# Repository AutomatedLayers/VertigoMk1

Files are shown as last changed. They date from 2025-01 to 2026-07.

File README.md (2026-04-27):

# VertigoMk1
## Automation for Makers

Vertigo Mk1 is a 3D printer designed for automation. Some of its distinct features include:
- A bed that rotates to a vertical position and scrapes printed parts off and out the bottom
- Print queues, batch jobs, and remote failure recovery
- A small footprint compared to other automated part removal systems
- Scraper modules that use afforable plastic razors that are easy to replace and won't damage the print surface
- A height-adjustable scraper bar that can hold different scraper moodules - including those designed by YOU
- The ability to print and remove parts made with various materials
- Compatibility with different magnetic print surfaces, i.e. PEI, PEO, PEY, Garolite/FR4/G10, etc. 
- The easily swappable and serviceable Hitchcock toolhead
- A reciprocating filament cutter under the extruder that won't get stuck while cutting
- Compatibility with multi-material and automatic filament replacement systems
- An elecronics backpack that can be easily accessed and serviced
- Source-available hardware and open source software

[LINK TO BOM](https://docs.google.com/spreadsheets/d/1A0MQrvO-RssSD-6shnWwc1etPSYvOc4fTYE_1AOMABk/edit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)

[LINK TO DOCS](https://automatedlayers.github.io/VertigoMk1/)

## The STL files and BOM are released for beta testing. We welcome suggestions through GitHub's isssue tracker. During this phase of the project, there may be some updates to the STLs and BOM, so check the [STL change history](https://github.com/AutomatedLayers/VertigoMk1/commits/main/hardware/STL) and the [BOM change history](https://github.com/AutomatedLayers/VertigoMk1/commits/main/hardware/BOM.csv)
____________________________________________
# [Kickstarter Has Funded!](https://www.kickstarter.com/projects/automatedlayers/vertigo-mk1-the-evolution-of-automated-3d-printing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)



[AutomatedLayers.com](https://automatedlayers.com)

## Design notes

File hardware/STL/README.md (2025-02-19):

# Notes on printing these parts

This printer is designed to use ASA printed parts and we strongly recommend using ASA or ABS to print the majority of these parts. ASA is [comparable to ABS](https://all3dp.com/2/asa-vs-abs-differences). Other materials may work however YMMV. There are a few parts that should be printed with another material, i.e. translucent light diffusers. 

ASA and ABS shrink after printing. Remeber to calibrate your slicer scaling settings for your specific filament's rate of shrinkage. I.E. We scale our parts up by ~0.8% when printing with Polylite ASA

Under Construction...

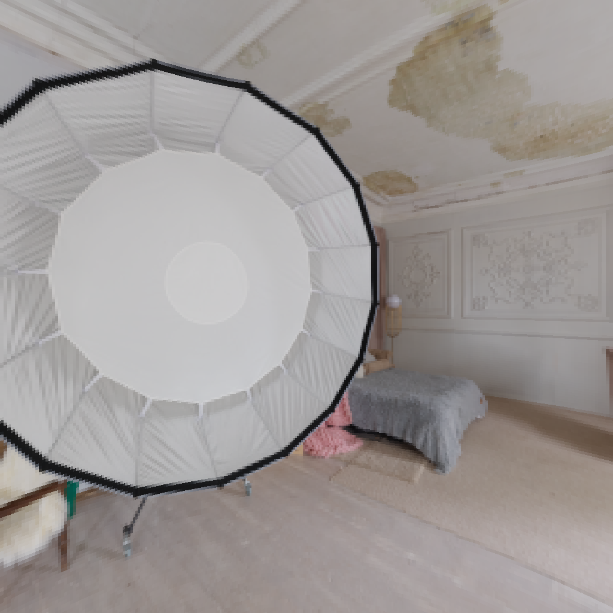
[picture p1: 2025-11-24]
docs/assets/js/o3dv/envmaps/studio/nx.png

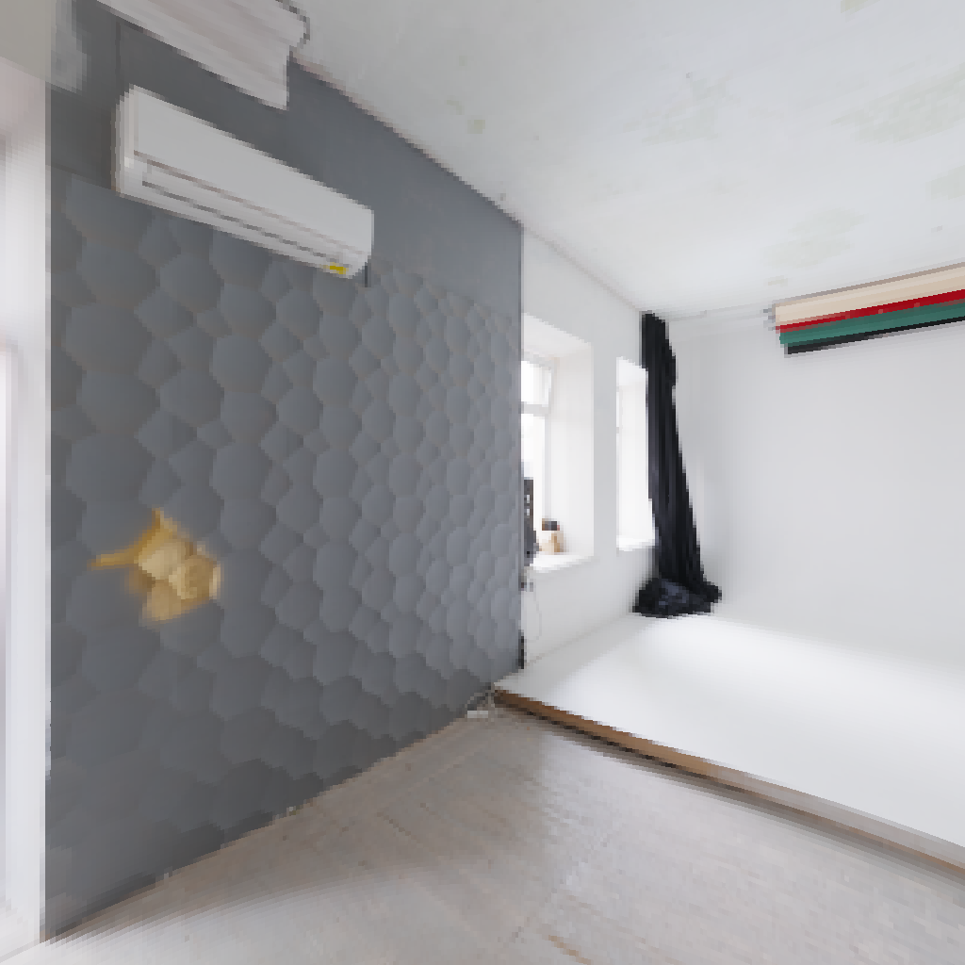
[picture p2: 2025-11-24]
docs/assets/js/o3dv/envmaps/studio/px.png

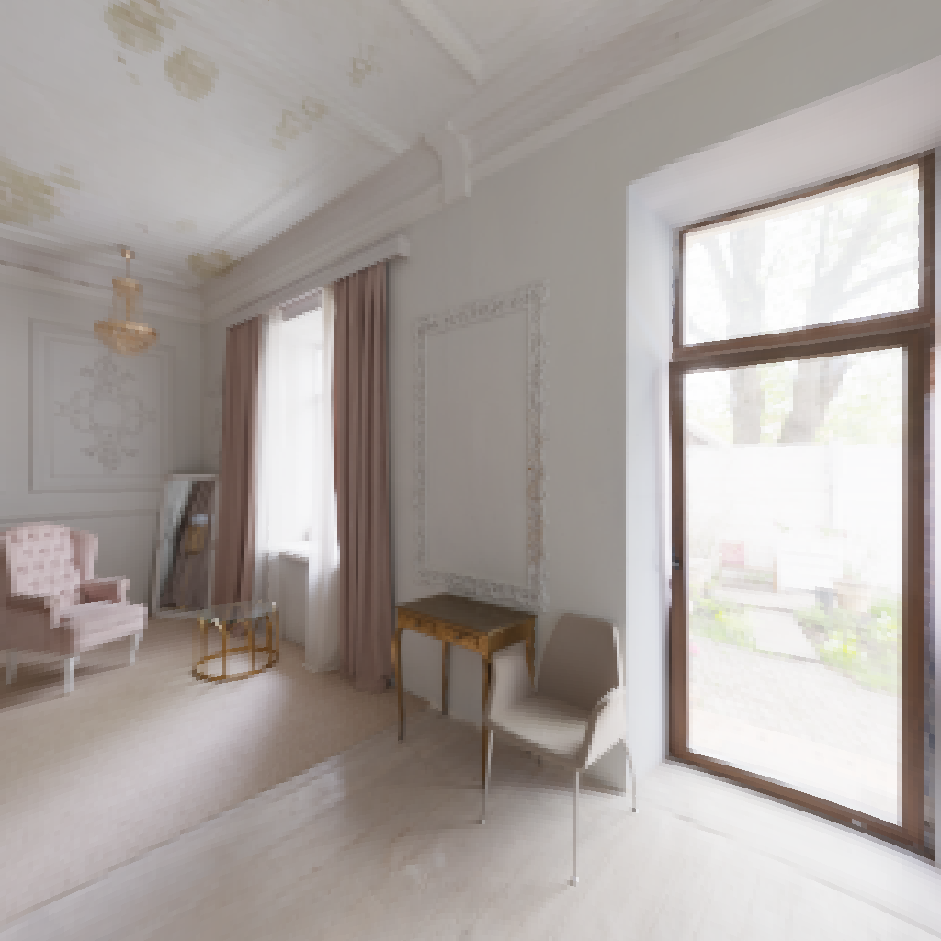
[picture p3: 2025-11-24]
docs/assets/js/o3dv/envmaps/studio/pz.png

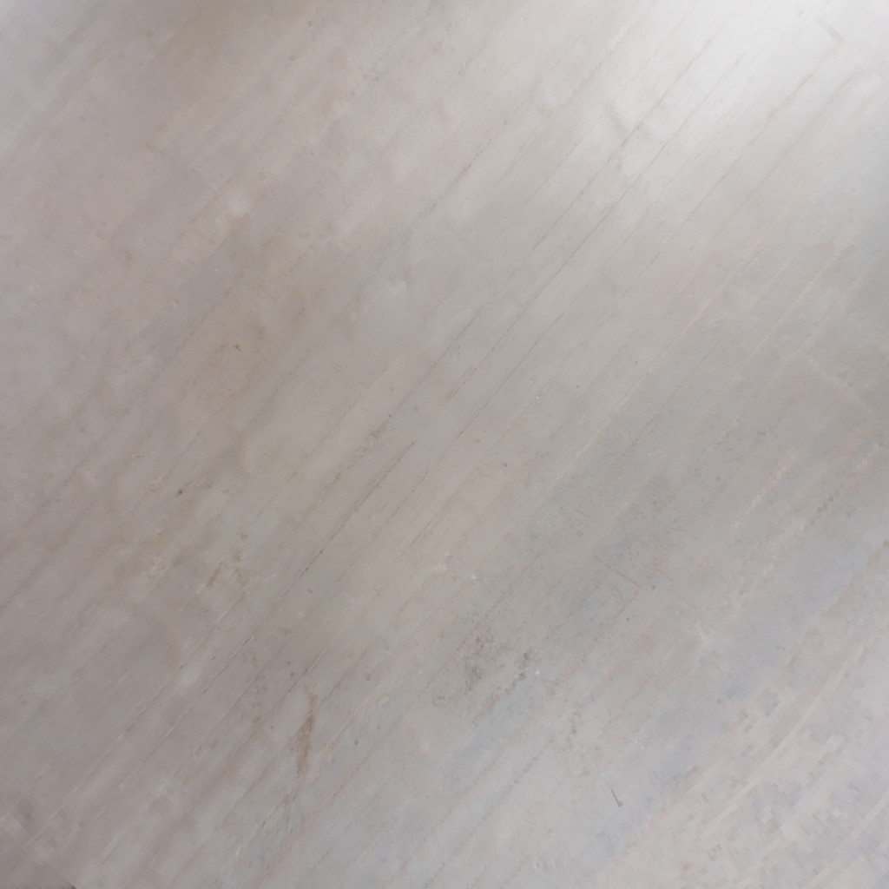
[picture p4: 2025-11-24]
docs/assets/js/o3dv/envmaps/studio/ny.png

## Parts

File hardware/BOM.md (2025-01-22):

[Link to BOM](https://docs.google.com/spreadsheets/d/10YGANyMZiwzZxh9XAjgCuSkIS7JlSp2upRrYD-nj4ag/edit?usp=sharing)

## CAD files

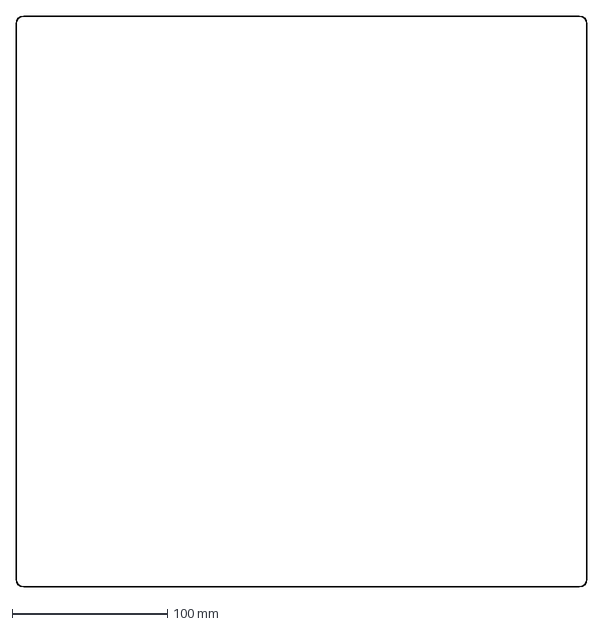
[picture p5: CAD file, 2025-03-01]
hardware/DXF/Top Panel.DXF
368.0 x 368.0 mm

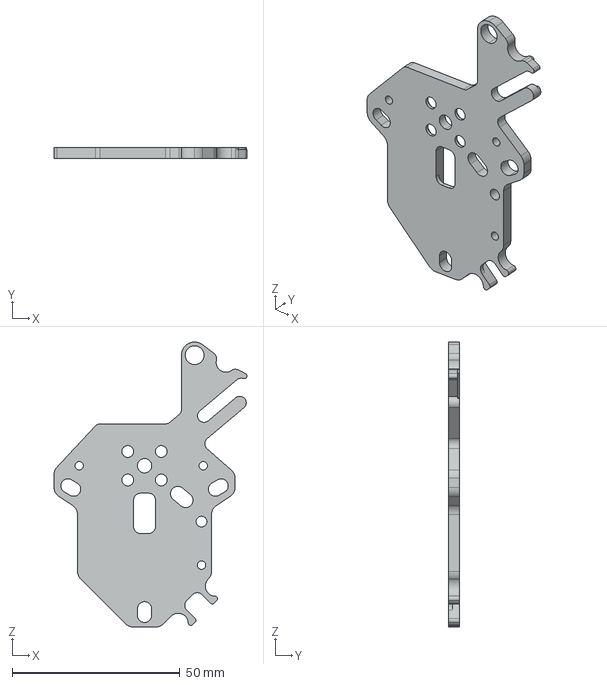
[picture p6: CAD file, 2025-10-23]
hardware/STEP/Toolhead Plate - CNC - Mild Steel 1045 - No Pockets - REV C.STEP
57.6 x 3.18 x 85.0 mm

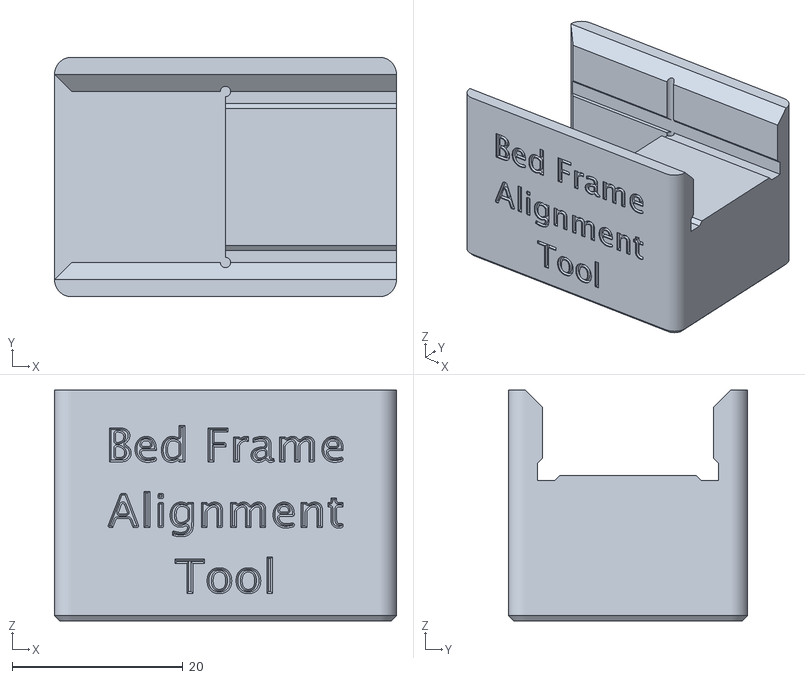
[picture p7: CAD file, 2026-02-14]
hardware/STL/00 Tools/Bed Frame Alignment Tool.stl
40.0 x 28.0 x 27.0

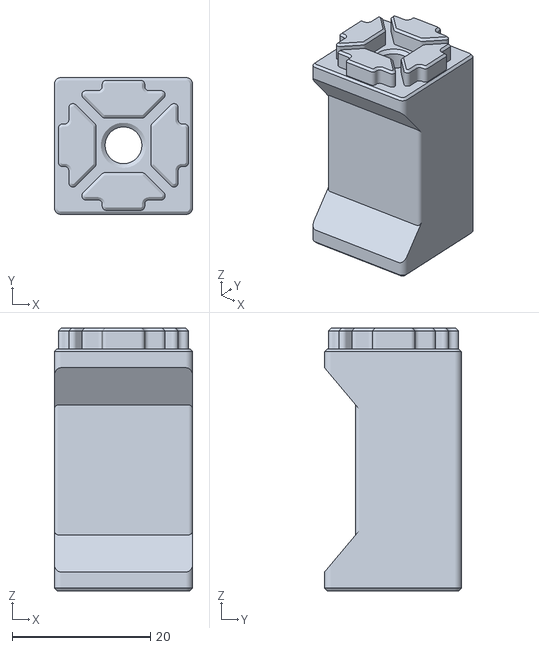
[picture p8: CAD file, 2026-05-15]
hardware/STL/01 Frame/Frame Post Connector - Q2 (LDO Profile).STL
20.0 x 19.8 x 38.0

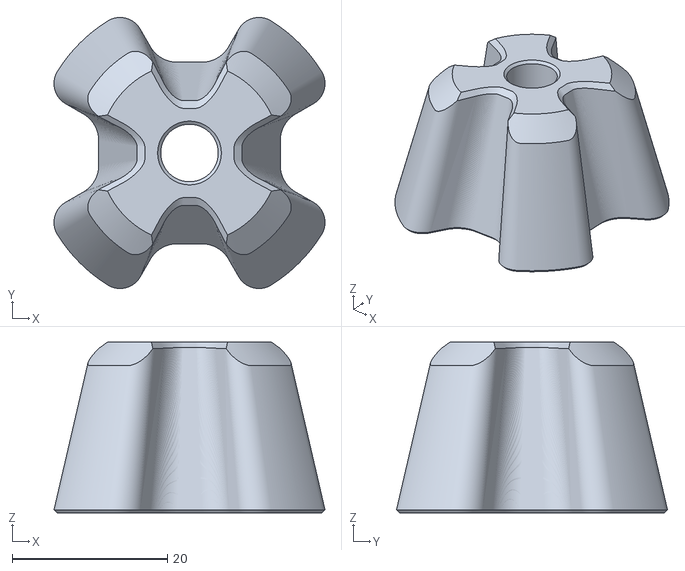
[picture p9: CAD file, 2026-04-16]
hardware/STL/02 Feet/All Feet/Foot Height Knob Cap - Accent - Q4.stl
34.9 x 34.9 x 22.0

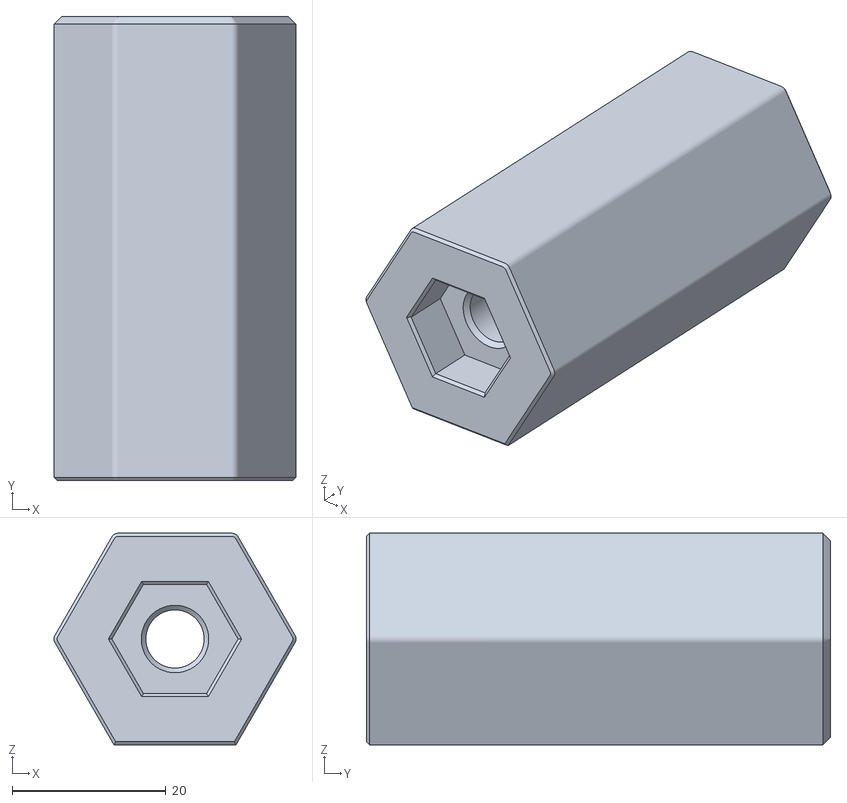
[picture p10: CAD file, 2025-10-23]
hardware/STL/02 Feet/Front Feet/Foot Front Replaceable Thread Plug - Q2.stl
31.4 x 60.3 x 27.5

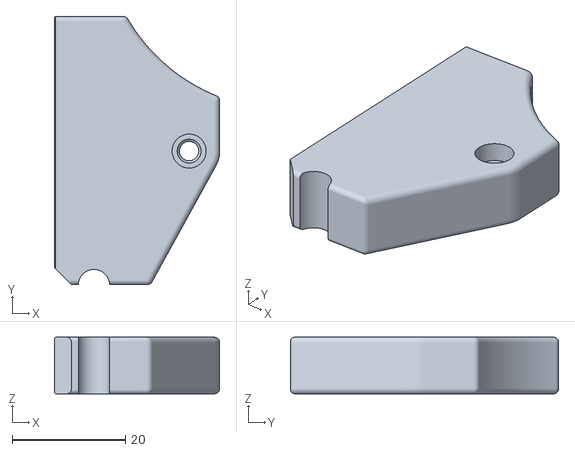
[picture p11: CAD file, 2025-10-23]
hardware/STL/02 Feet/Rear Feet/Foot Rear A Logo Nugget - Accent - Multi.stl
29.2 x 47.3 x 10.0

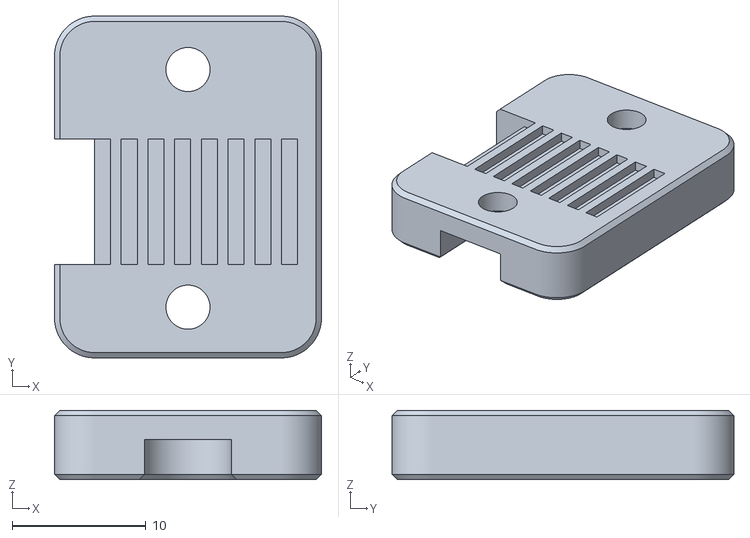
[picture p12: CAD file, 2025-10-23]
hardware/STL/03 Z Joints/Belt Clamps/Belt Clamp Top - Accent - Q4.stl
20.0 x 25.6 x 5.20

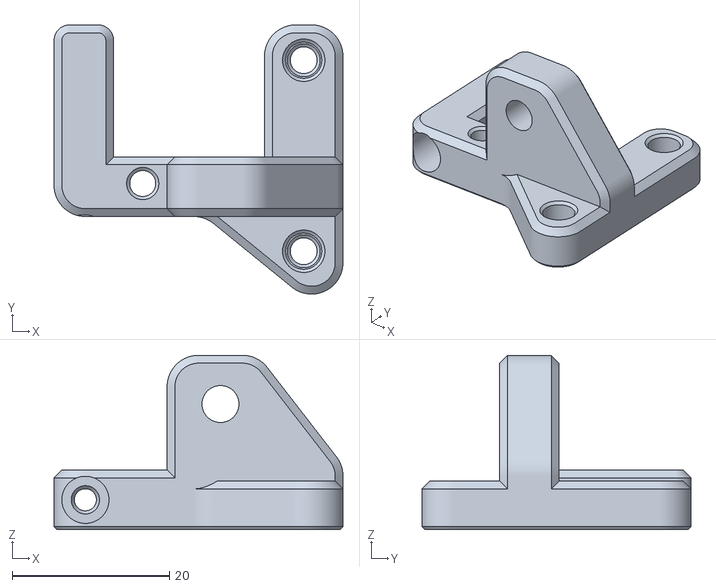
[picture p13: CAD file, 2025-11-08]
hardware/STL/03 Z Joints/Front Z Joints/Front Joint B - Endstop Adjustment.stl
36.8 x 34.3 x 22.2

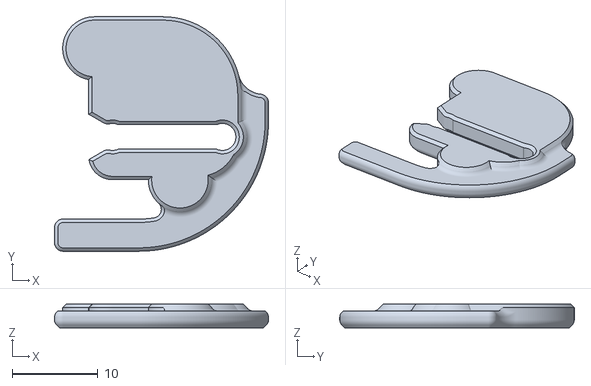
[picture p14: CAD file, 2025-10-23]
hardware/STL/03 Z Joints/Rear Z Joints/Rear Joint B - Seatbelt Lock B.stl
25.0 x 27.4 x 2.80

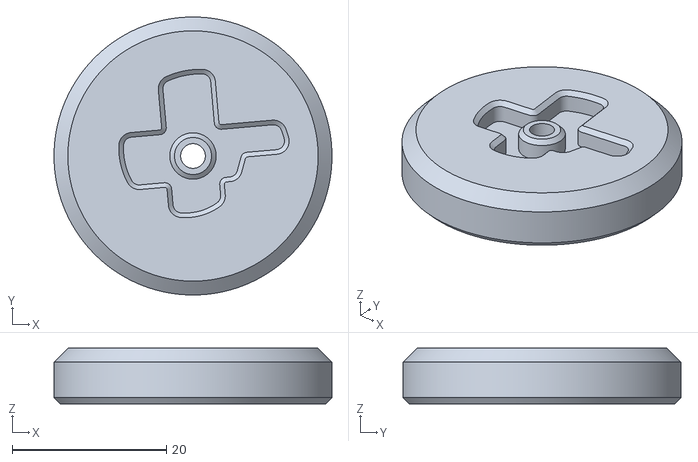
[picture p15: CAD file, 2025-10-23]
hardware/STL/04 XY Gantry/XY Drives/XY Drive B Cam Cap - Accent.stl
36.0 x 36.0 x 7.20

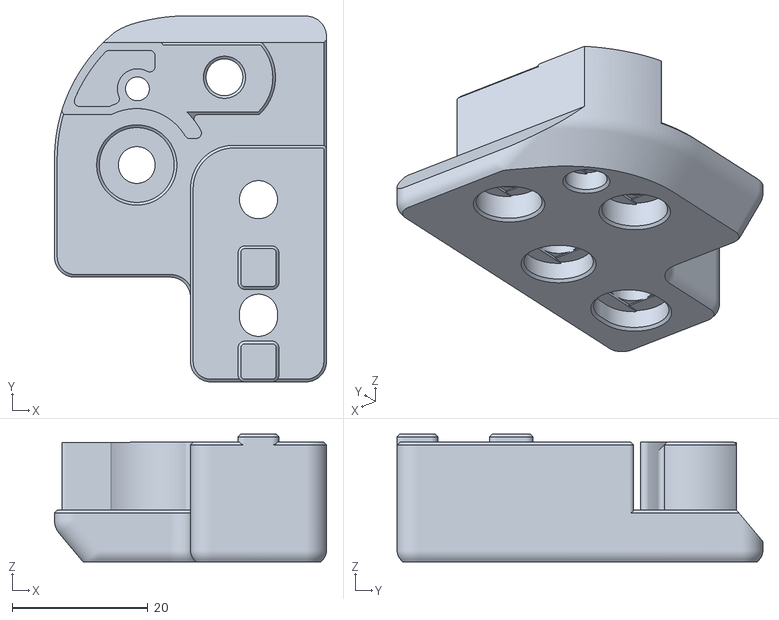
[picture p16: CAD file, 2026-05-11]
hardware/STL/04 XY Gantry/XY Joints/XY Joint B - Top.stl
40.0 x 53.8 x 18.8

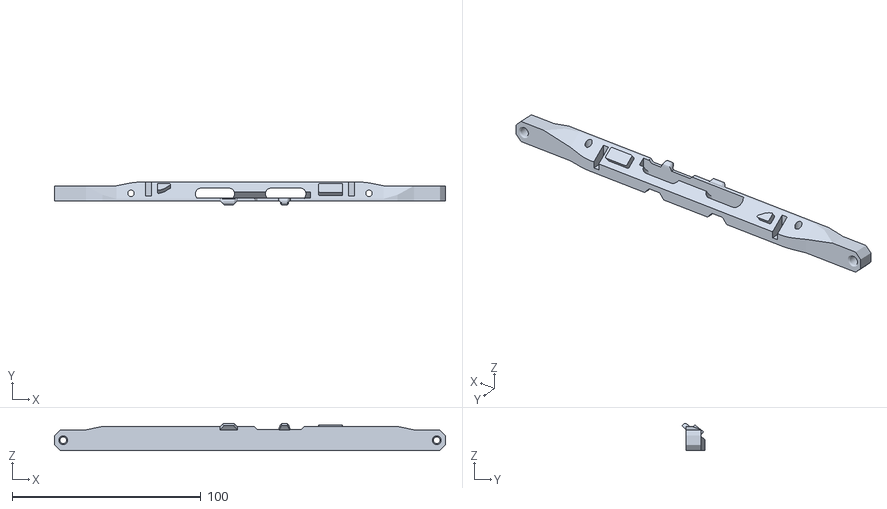
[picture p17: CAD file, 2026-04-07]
hardware/STL/05 Top Module/Camera and Logo Light/Logo LED & Camera Mount.stl
207.0 x 12.2 x 14.4

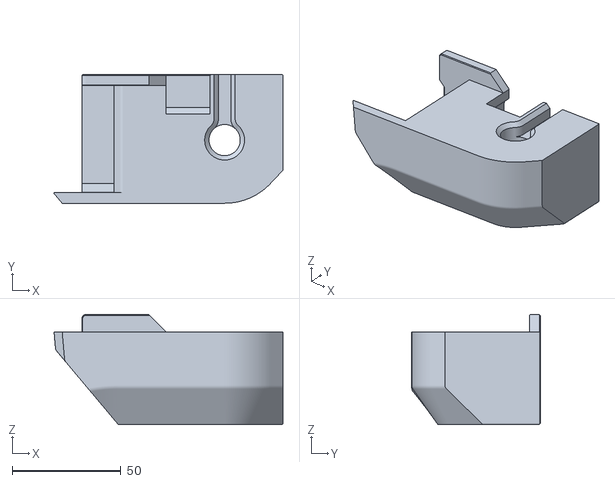
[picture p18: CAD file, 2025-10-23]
hardware/STL/05 Top Module/Facades/Motor Facade Front B.stl
105.1 x 59.0 x 50.6

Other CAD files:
hardware/STL/05 Top Module/Top Panel Plate/Top Panel Plate.stl
hardware/STL/05 Top Module/Z Drives/Z Drive Housing Cap B - Q2.stl
hardware/STL/06 Bed Platform/Bed Frame/Bed Frame - Tool Ball Mount B.stl
hardware/STL/06 Bed Platform/Scraper Bar/Scraper Bar Wing A.stl
hardware/STL/00 Tools/Bed Chain Cable Setter Tool.STL
hardware/STL/00 Tools/Force Sensor Washer Setting Tool.stl
hardware/STL/00 Tools/Frame Rear Bar Alignment Tool.STL
hardware/STL/00 Tools/Idler Bearing Tool.stl
hardware/STL/00 Tools/Light Bar Offset Tool.STL
hardware/STL/00 Tools/MGN9 Alignment Tool - Q2.STL
hardware/STL/00 Tools/Rear Foot Roll-In Nut Alignment Tool.STL
hardware/STL/00 Tools/XY Drive Roll-In Nut Alignment.STL
hardware/STL/00 Tools/Y-Rail Offset Tool.STL
hardware/STL/00 Tools/Z Drive Roll-In Nut Alignment Tool.STL
hardware/STL/01 Frame/Frame Post Connector - Q2 (Old).STL
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

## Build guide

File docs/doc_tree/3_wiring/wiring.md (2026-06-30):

---
title: Wiring
layout: default
nav_order: 3
zoom_images: true
---

# Wiring

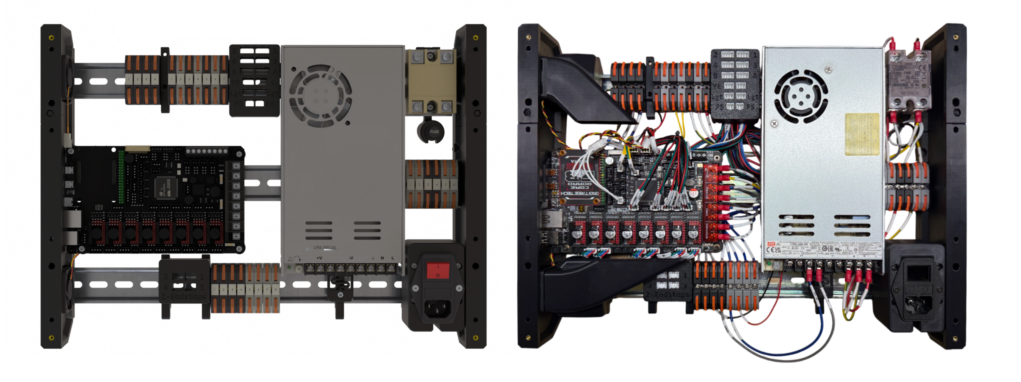
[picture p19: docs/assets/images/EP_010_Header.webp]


## Before You Start

The goal of this guide is to help you wire the printer carefully and consistently. That said, **electricity _can_ be dangerous**. Incorrect wiring or unsafe work practices can cause injury, damage components, start a fire, or worst of all, frighten your kitty. **You’ve got this — take your time, work safely, don’t skip steps, and double-check each step before moving forward.**

This printer is a DIY kit assembled from parts sourced from many suppliers across the world. Because of this, **hardware details may vary** between supplier batches or self-sourced parts. This can include component pinout, wire colors, connector styles, and other small differences. **Be careful about making assumptions based on appearance alone.** This guide provides the tools needed to verify each part, cable, and connection using the specification documents, which will be explained in the next section.

{: .important }
Some image text may appear small on this page. For a larger view, right-click the image and select "Open image in new tab".

{: .note}
[BigTreeTech Manta M8P V2 Documentation](https://github.com/bigtreetech/Manta-M8P/blob/master/V2.0/BIGTREETECH%20MANTA%20M8P%20V2.0%20User%20Manual.pdf) contains information related to the printer controller (mainboard). For convenience, here's the [M8P V2 Pinout]({{site.url}}/{{site.baseurl}}/assets/images/m8pv2_pinout.webp).

{: .note}
[Mellow FLY SHT36 V3 Documentation](https://mellow.klipper.cn/en/docs/ProductDoc/ToolBoard/fly-sht36/sht36_v3/) contains information related to the toolhead board. For convenience, here's the [FLY SHT36 V3 Pinout]({{site.url}}/{{site.baseurl}}/assets/images/sht36v3_pinout.webp)

## Table of Contents

- [Wiring](#wiring)
  - [Before You Start](#before-you-start)
  - [Table of Contents](#table-of-contents)
  - [Understanding the Wiring Diagram and Cable Spec](#understanding-the-wiring-diagram-and-cable-spec)
    - [The Cable Specification](#the-cable-specification)
      - [Cable Construction Examples](#cable-construction-examples)
    - [The Wiring Diagram](#the-wiring-diagram)
      - [Finding Z-Code Termination Points Example](#finding-z-code-termination-points-example)
  - [Diagrams of Peripheral-Board Connections, Z-Codes, and Schematic Labels](#diagrams-of-peripheral-board-connections-z-codes-and-schematic-labels)
  - [Configuring the Toolhead Board](#configuring-the-toolhead-board)
    - [Install Jumpers and Fan Mosfet and Set Switches (for CAN Mode) on Toolhead Board](#install-jumpers-and-fan-mosfet-and-set-switches-for-can-mode-on-toolhead-board)
  - [Wiring The Electronics Backpack](#wiring-the-electronics-backpack)
    - [1. Install CM and Heatsink](#1-install-cm-and-heatsink)
    - [2. Install Jumpers on Main Board](#2-install-jumpers-on-main-board)
    - [3. Install Stepper Drivers](#3-install-stepper-drivers)
    - [4. Install Terminal Block Bus Bars](#4-install-terminal-block-bus-bars)
    - [5. Install Terminal Block Bus Bar Fasteners](#5-install-terminal-block-bus-bar-fasteners)
    - [6. Install Terminal Block Number Covers](#6-install-terminal-block-number-covers)
    - [7. Check Fuse Amperage - IEC C14 Plug](#7-check-fuse-amperage---iec-c14-plug)
    - [8. Check Fuse Amperage - Bed Fuse (Z-07)](#8-check-fuse-amperage---bed-fuse-z-07)
    - [9. Check PSU's AC Input Voltage Switch](#9-check-psus-ac-input-voltage-switch)
    - [10. Install Cables: Z-01, Z-02, Z-03, Z-11, Z-12](#10-install-cables-z-01-z-02-z-03-z-11-z-12)
    - [11. Install Cables: Z-04, Z-05, Z-06](#11-install-cables-z-04-z-05-z-06)
    - [12. Prepare Multimeter for Continuity Checks](#12-prepare-multimeter-for-continuity-checks)
    - [13. Check for short between AC Live (L) and AC Neutral (N)](#13-check-for-short-between-ac-live-l-and-ac-neutral-n)
    - [14. Check for short between AC Neutral (N) and AC Earth (⏚)](#14-check-for-short-between-ac-neutral-n-and-ac-earth-)
    - [15. Check for short between AC Live (L) and AC Earth (⏚)](#15-check-for-short-between-ac-live-l-and-ac-earth-)
    - [16. Check for short between PSU's DC(+) and DC(-)](#16-check-for-short-between-psus-dc-and-dc-)
    - [17. Check for continuity between IEC C14 plug and PSU for AC Live (L)](#17-check-for-continuity-between-iec-c14-plug-and-psu-for-ac-live-l)
    - [18. Check for continuity between IEC C14 plug and PSU for AC Neutral (N)](#18-check-for-continuity-between-iec-c14-plug-and-psu-for-ac-neutral-n)
    - [19. Check for continuity between IEC C14 plug and PSU for AC Earth (⏚)](#19-check-for-continuity-between-iec-c14-plug-and-psu-for-ac-earth-)
    - [20. Preparing for First Power ON](#20-preparing-for-first-power-on)
    - [Always prioritize your safety and the safety of those around you](#always-prioritize-your-safety-and-the-safety-of-those-around-you)
    - [21. Adjusting PSU to 24V](#21-adjusting-psu-to-24v)
    - [22. Install Terminal Block Covers](#22-install-terminal-block-covers)
    - [23. Install Cables: Z-13, Z-15, Z-17, Z-19](#23-install-cables-z-13-z-15-z-17-z-19)
    - [24. Install Cables: Z-14, Z-16, Z-18, Z-20](#24-install-cables-z-14-z-16-z-18-z-20)
    - [25. Install Cables: Z-07, Z-08, Z-09, Z-10, Z-21, Z-22](#25-install-cables-z-07-z-08-z-09-z-10-z-21-z-22)
    - [26. Install Cables: Z-23, Z-24, Z-26](#26-install-cables-z-23-z-24-z-26)
    - [27. Assembling Peripheral Blocks](#27-assembling-peripheral-blocks)
    - [28. Install Cables: Z-42, Z-43, Z-44, Z-45](#28-install-cables-z-42-z-43-z-44-z-45)
    - [29. Install Cables: Z-27, Z-28](#29-install-cables-z-27-z-28)
    - [30. Install Cables: Z-34, Z-35, Z-32/33](#30-install-cables-z-34-z-35-z-3233)
    - [31. Install Cables: Z-29, Z-30, Z-31](#31-install-cables-z-29-z-30-z-31)
    - [32. Install Cables: Z-40, Z-41](#32-install-cables-z-40-z-41)
    - [33. Install Cables: Z-38, Z-39](#33-install-cables-z-38-z-39)
    - [34. Install Cables: Z-36, Z-37](#34-install-cables-z-36-z-37)
    - [35. Complete the Electronics Backpack Section then Continue](#35-complete-the-electronics-backpack-section-then-continue)
    - [36. Install Cables: Z-25, Z-48, Z-49, Z-53, Z-54, Z-55, Z-56, Z-60, Z-61, Z-114](#36-install-cables-z-25-z-48-z-49-z-53-z-54-z-55-z-56-z-60-z-61-z-114)
    - [37. Unplug Toolhead's XT30 Connector](#37-unplug-toolheads-xt30-connector)
    - [38. Checking Toolhead Power](#38-checking-toolhead-power)
    - [39. PZ Probe Controller Cable: Z-105, Z-106, Z-107](#39-pz-probe-controller-cable-z-105-z-106-z-107)
    - [40. Install Lights, Endstops, Electronics Fans, Camera: Z-57, Z-58, Z-59, Z-68, Z-69, Z-70, Z-71, Z-72, Z-77, Z-78, Z-116](#40-install-lights-endstops-electronics-fans-camera-z-57-z-58-z-59-z-68-z-69-z-70-z-71-z-72-z-77-z-78-z-116)
    - [41. Endstop Check](#41-endstop-check)
    - [42. Electronics Fans Pinout Check: Z-77, Z-78](#42-electronics-fans-pinout-check-z-77-z-78)
    - [43. Install Bed Heater, Bed Fans: Z-46, Z-47, Z-50, Z-51, Z-52](#43-install-bed-heater-bed-fans-z-46-z-47-z-50-z-51-z-52)
    - [44. Install Stepper Motors: Z-46, Z-47, Z-50, Z-51, Z-52](#44-install-stepper-motors-z-46-z-47-z-50-z-51-z-52)
  - [Continue to the Firmware Guide](#continue-to-the-firmware-guide)

## Understanding the [Wiring Diagram and Cable Spec](https://github.com/AutomatedLayers/VertigoMk1/tree/main/electrical/Cable%20Spec%20%26%20Wiring%20Diagram)

Wiring is defined by two core documents: the **wiring diagram** and the **cable specification**.

### The Cable Specification

This document defines how each cable is manufactured, including its Z-code, length, wire gauge, color, pinout, and other relevant build details.

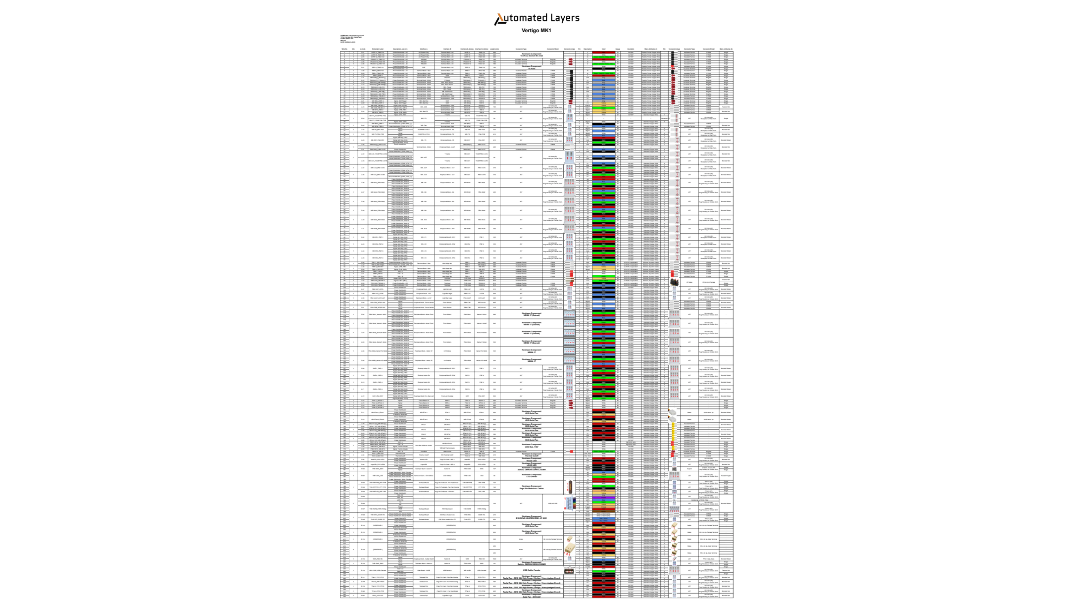
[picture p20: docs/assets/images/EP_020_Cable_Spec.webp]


<br>

#### Cable Construction Examples

Below are cables Z-11 and Z-36 as it appears in the cable specification, along with a photos of the construction for reference. Keep in mind that not every hardware component will have the physical Z-code label attached. In those cases, identify the cable by comparing its features to the cable specification, or consult the Wiring Diagram if you know where the component is being installed to easier identifiy the Z-code. 

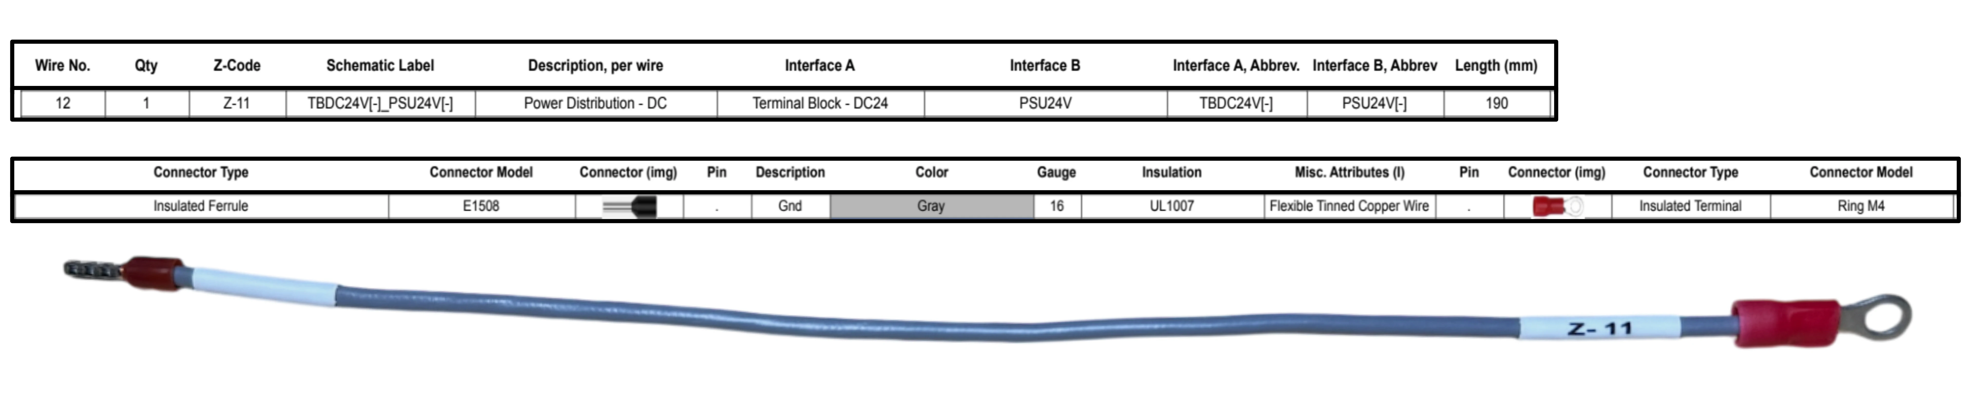
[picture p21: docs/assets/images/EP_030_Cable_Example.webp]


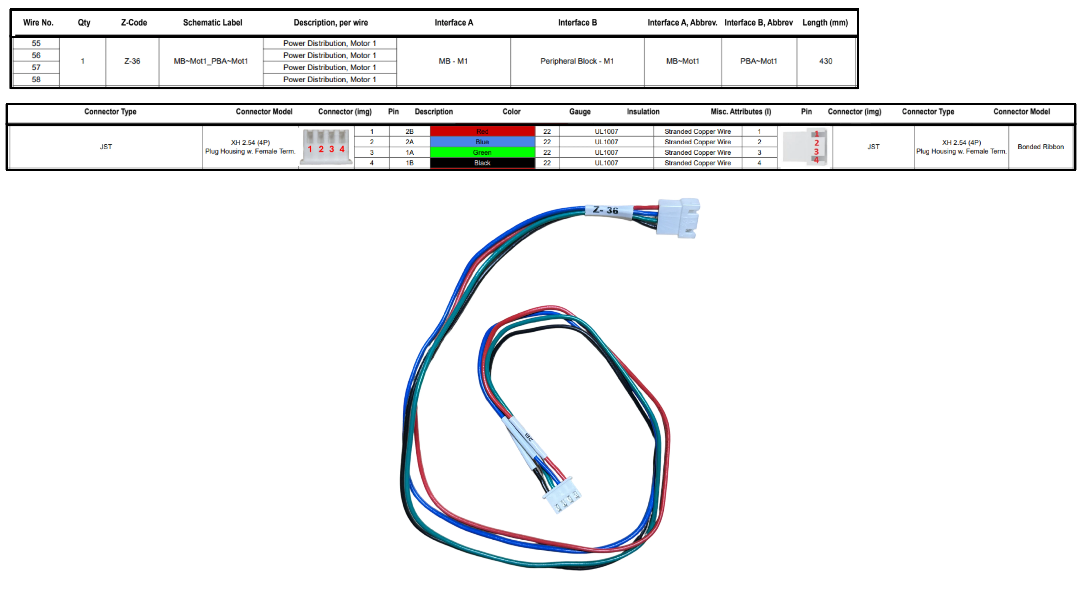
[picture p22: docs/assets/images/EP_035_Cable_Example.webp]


### The Wiring Diagram

This document defines how the cables terminate within the system, using symbols and Z-codes to identify connections.

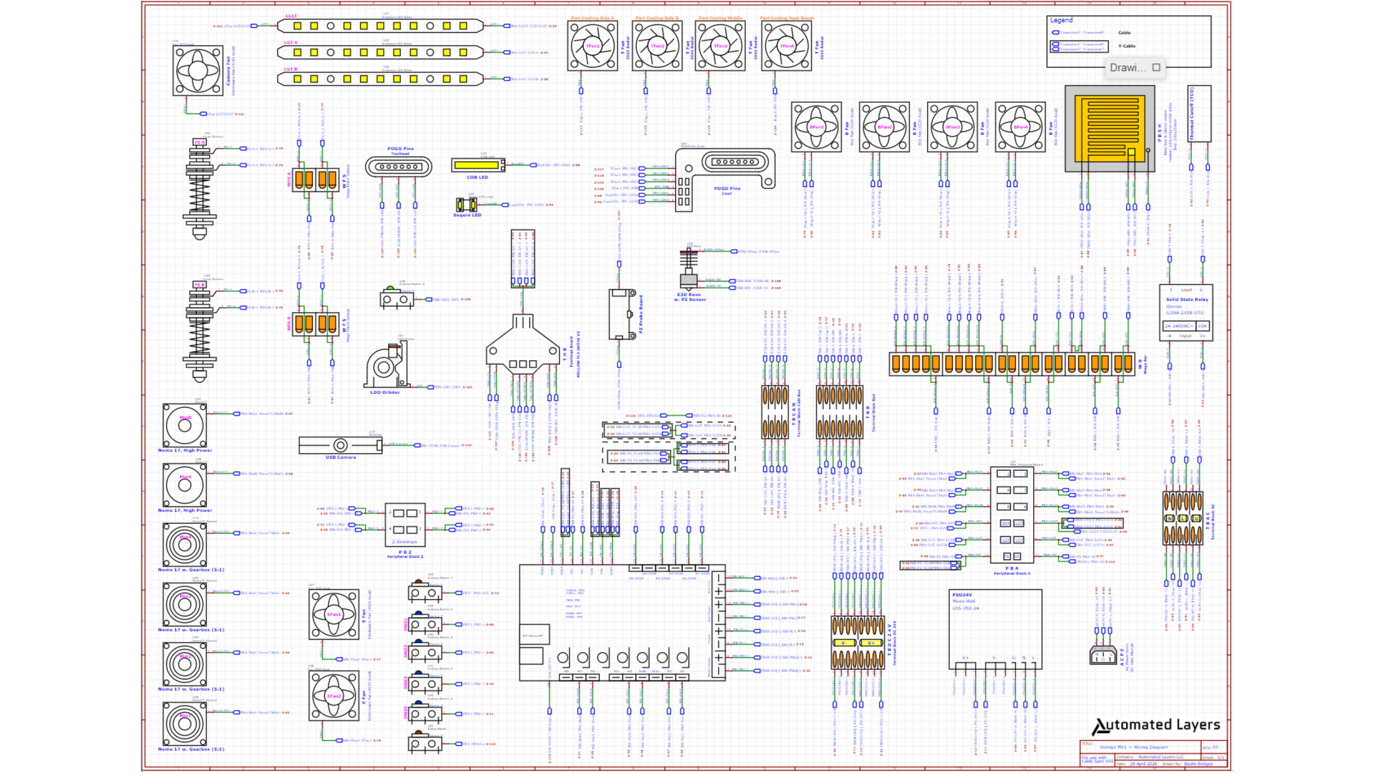
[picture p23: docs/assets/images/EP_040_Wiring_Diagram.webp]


<br>

#### Finding Z-Code Termination Points Example

* Locate the Z-Code: There will be one located at each termination point for the cable
* Note the schematic label: This indicates the termination points using abbreviated names, separated by an underscore "_"
  * E.g. Z-11, TBDC24V[-]_PSU24V[-] indicates you can find the termination points at Terminal Block DC 24V [-] and the Power Supply Unit 24V [-]

**Tip:** Opening the PDF and using the find function is an easy way to navigate the Z-Code termination points.

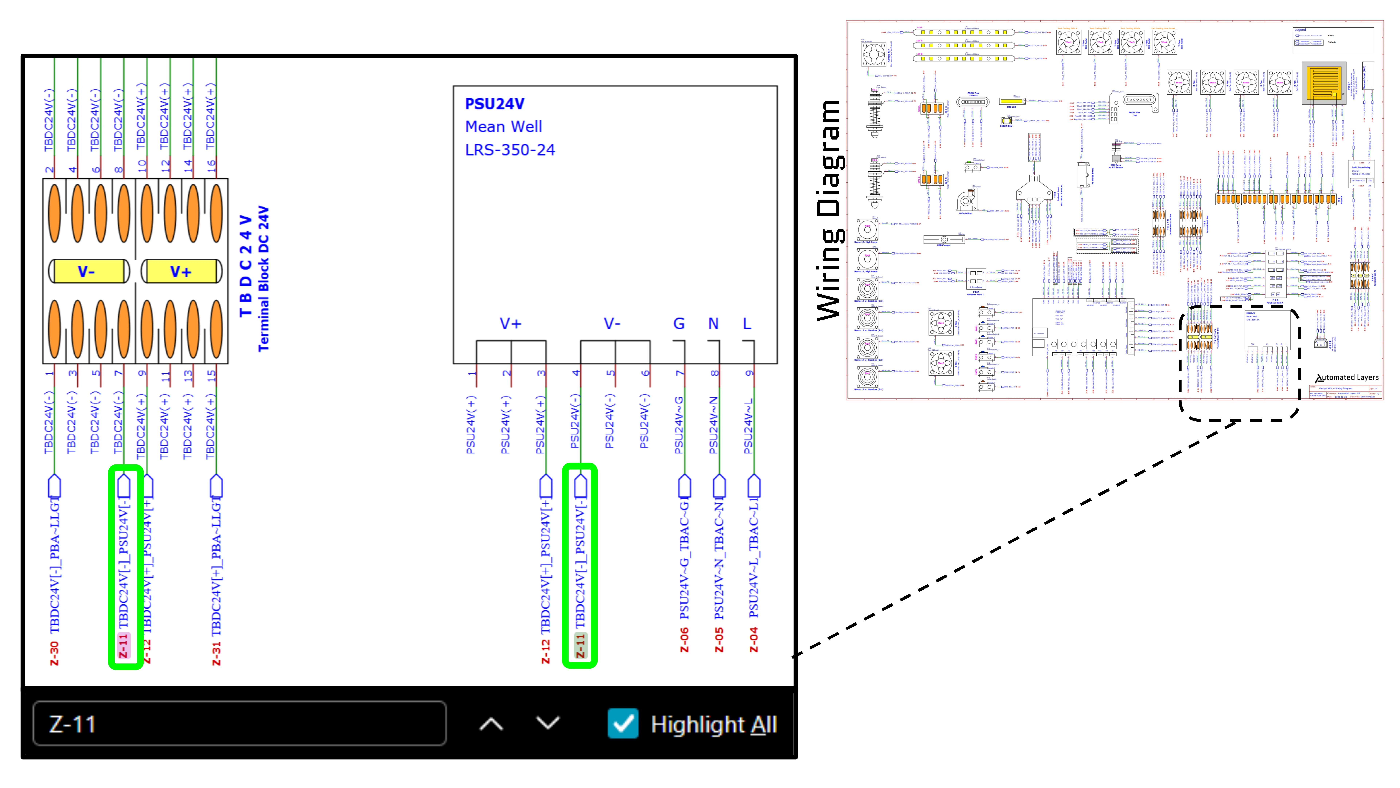
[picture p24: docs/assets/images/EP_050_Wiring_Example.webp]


{: .warning }
When using these documents, always perform a quick check to confirm that you are using the [latest revision](https://github.com/AutomatedLayers/VertigoMk1/tree/main/electrical/Cable%20Spec%20%26%20Wiring%20Diagram) before proceeding.

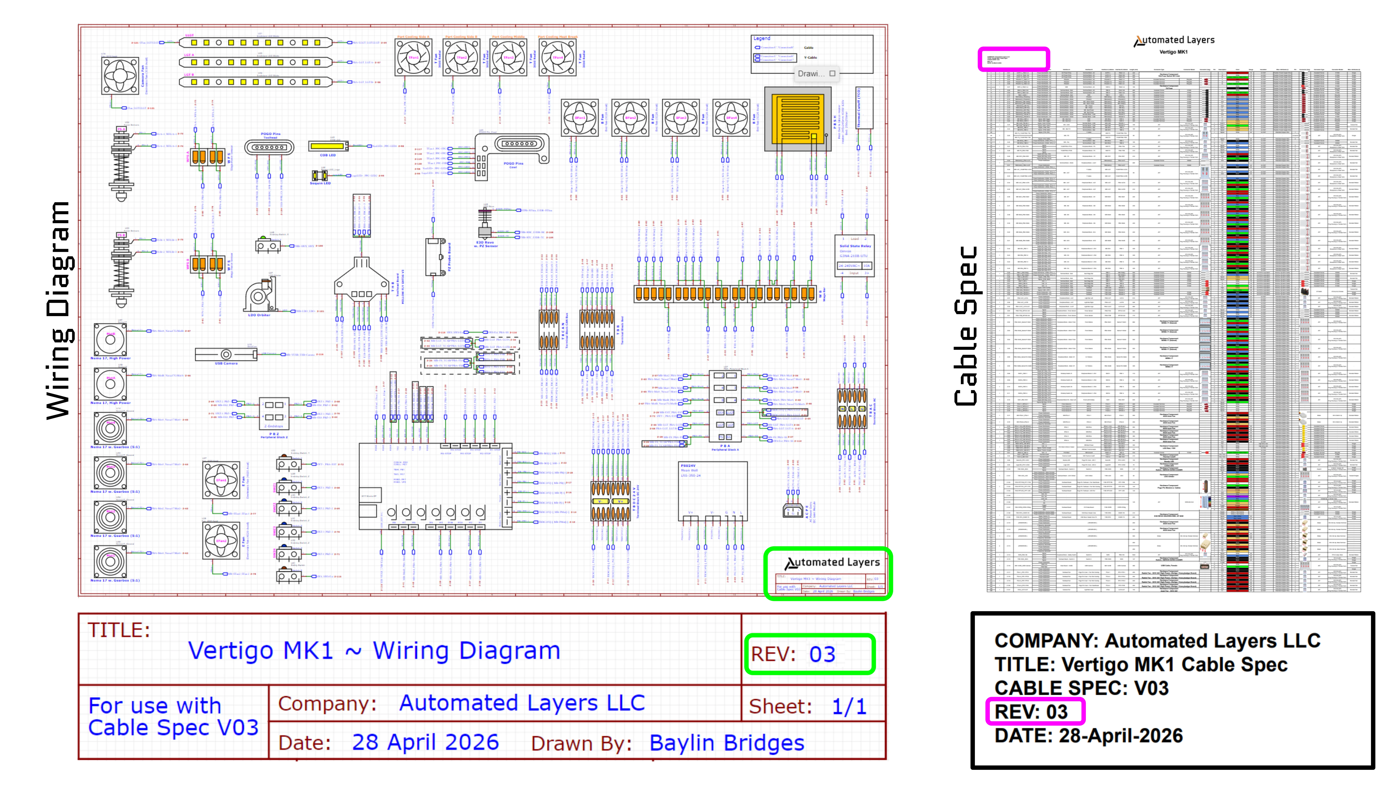
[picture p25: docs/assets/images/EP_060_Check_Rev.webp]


<br>

## Diagrams of Peripheral-Board Connections, Z-Codes, and Schematic Labels

<br>







<br>

[Return to Z Endstop assembly]({{site.url}}/{{site.baseurl}}/doc_tree/2_assembly/06_auxiliary_modules_1/1_z-endstops.html)

## Configuring the Toolhead Board

### Install Jumpers and Fan Mosfet and Set Switches (for CAN Mode) on Toolhead Board

* Toolhead fans are set to 24V
* Setting GPIO20 to 3.3V is optional, but recommended
* Fan Mosfet is installed (Mosfet can be installed either orientation; just ensure all 6 pins are inserted)
* Toolhead board is set to CAN mode with switches on back of board
* Set CAN Bus 120 Ohm terminal resistor to ON position

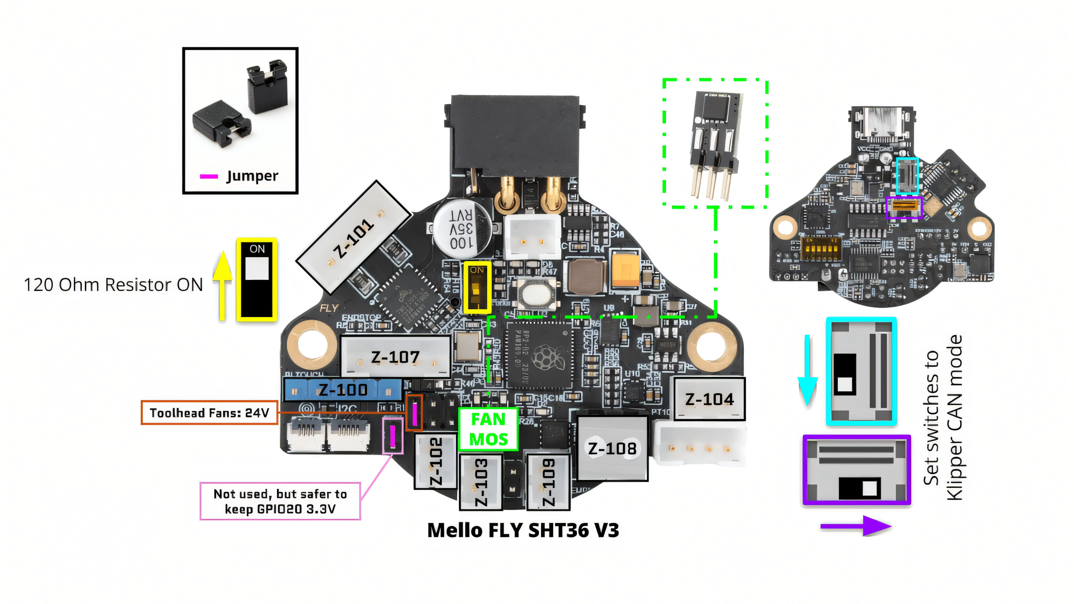
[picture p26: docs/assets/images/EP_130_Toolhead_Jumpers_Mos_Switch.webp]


[Return to Extruder Plate assembly]({{site.url}}/doc_tree/2_assembly/12_toolhead/1_extruder_plate.html)

## Wiring The Electronics Backpack

<!-- ### If this is your first visit, you are arriving from "[Assembly - Electronics Backpack - Vertigo MK1](https://youtu.be/X98VDksNd48?si=4Hsjn2eWTSBX0ba6)"

![]({{site.url}}/{{site.baseurl}}/assets/images/EP_090_Youtube_Electronics_Backpack.webp) -->

### 1. Install CM and Heatsink

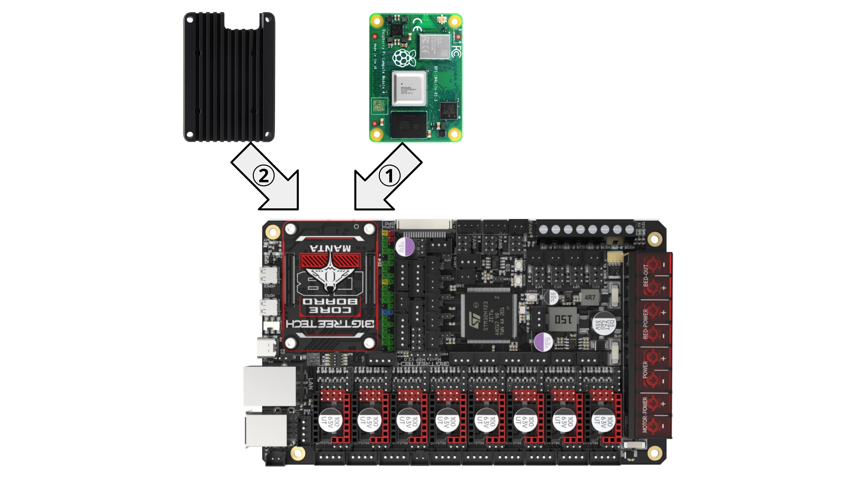
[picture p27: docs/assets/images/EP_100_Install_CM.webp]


### 2. Install Jumpers on Main Board

**Jumpers are used to select the following settings:**

* All stepper drivers are set to 24V
* TMC5160T Pro drivers are set to SPI mode
* TMC2209 drivers are set to UART mode
* Bed fans are set to 24V
* E-Panel fans are set to 24V
* Enclosure LEDs are set to 24V
* CAN Bus 120 ohm jumper is installed (*smaller jumper than the others)

{: .warning }
Double-check all jumper settings before applying power — an incorrect configuration can permanently damage the board (the kind that can't be undone). We can tell you from experience an extra or misplaced jumper makes for a good firework show. 

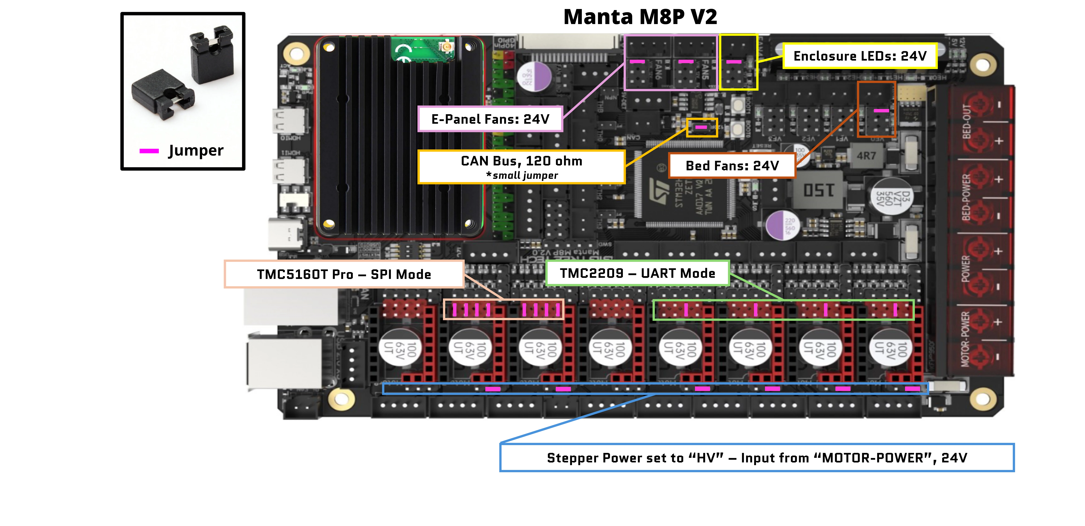
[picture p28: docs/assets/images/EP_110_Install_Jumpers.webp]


### 3. Install Stepper Drivers

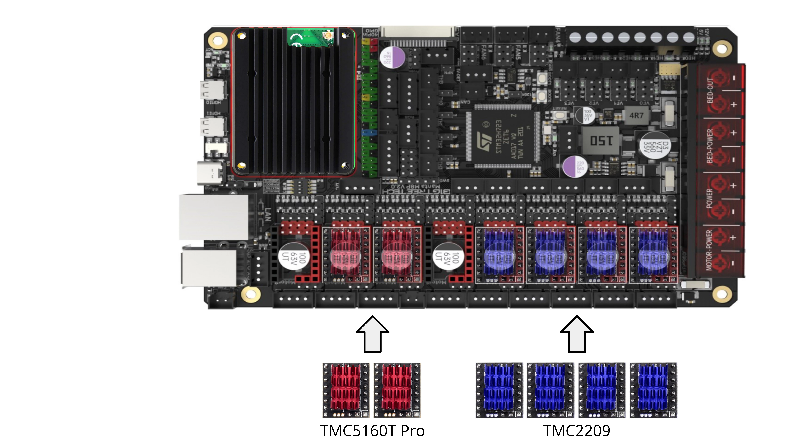
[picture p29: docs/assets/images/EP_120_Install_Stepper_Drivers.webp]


### 4. Install Terminal Block Bus Bars

* Cut terminal block bus bars to length
* Trim excess material from where the cut was made
* Install bus bars in terminal blocks as shown

{: .warning }
Double-check that each bus bar is cut to the correct node length. Trim any excess material between bus bars so they are not close to touching. When finished, it should match the image above.

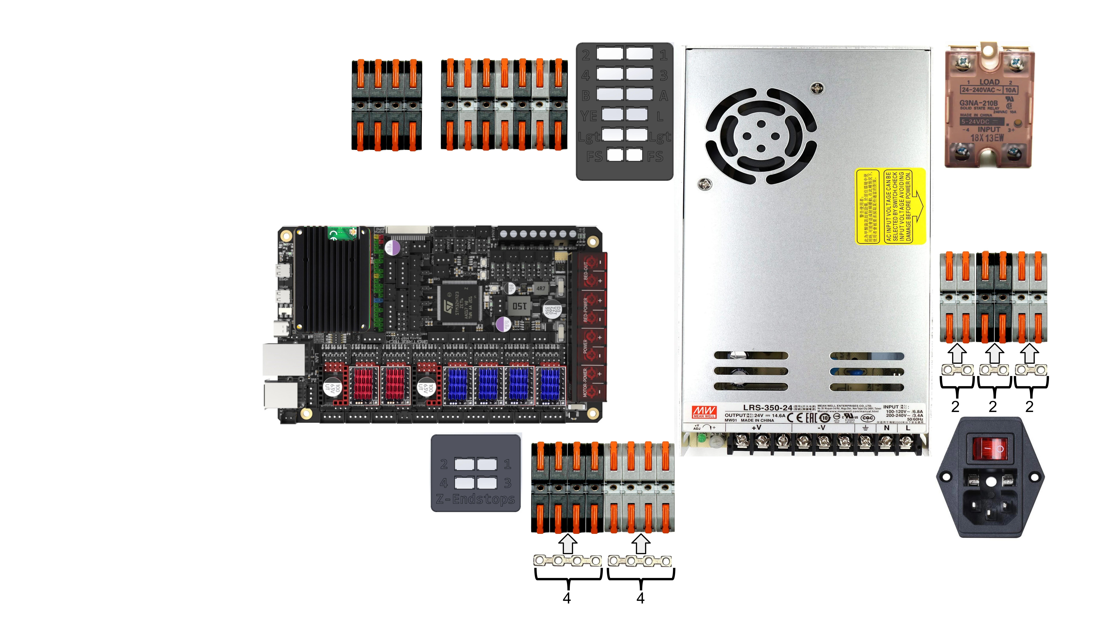
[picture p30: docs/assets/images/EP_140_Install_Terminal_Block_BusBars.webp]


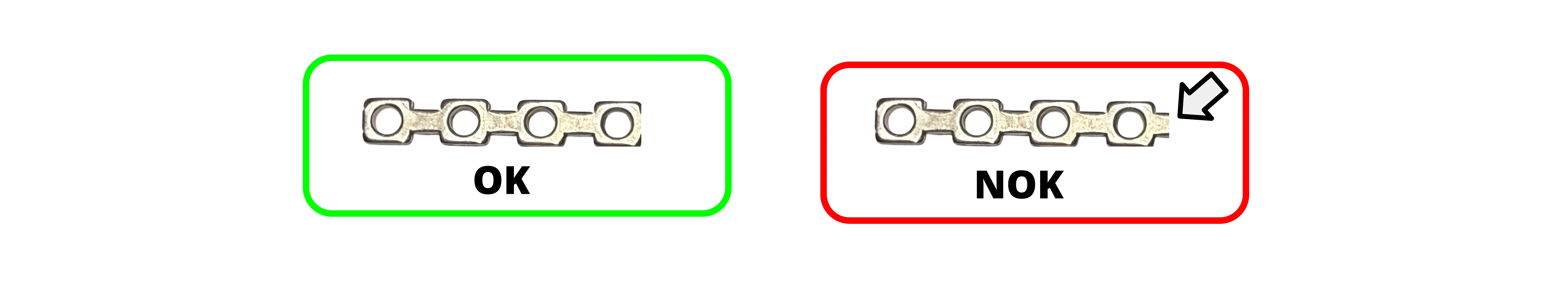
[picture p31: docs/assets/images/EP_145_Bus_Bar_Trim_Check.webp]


### 5. Install Terminal Block Bus Bar Fasteners

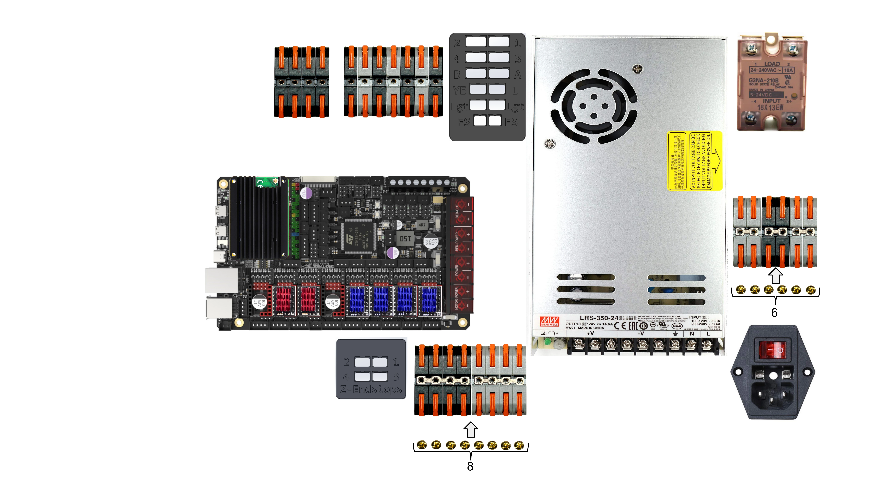
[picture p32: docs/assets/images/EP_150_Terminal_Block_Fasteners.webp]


### 6. Install Terminal Block Number Covers

* Install terminal block number covers for Terminal Block CAN (TBCAN) and Terminal Block Bed (TBB)
* We will leave the others uncovered for the next steps

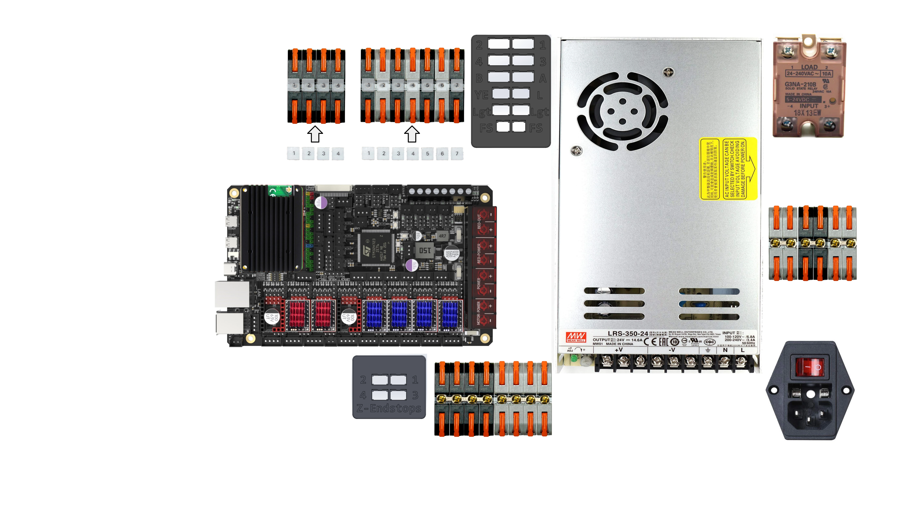
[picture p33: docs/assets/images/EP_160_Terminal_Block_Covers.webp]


### 7. Check Fuse Amperage - IEC C14 Plug

* This step is a safety check to make sure the components have the correct fuse sizes for your region.
* Remove the fuse and verify that the amperage rating matches the value listed in the table.
* Re-install the fuse

{: .warning }
Do not assume the installed fuses are correct. An oversized fuse may not blow when a fault occurs, which can allow wires or components to overheat. This can damage the printer, create a fire hazard, or cause serious injury. Always verify the fuse size before applying power.

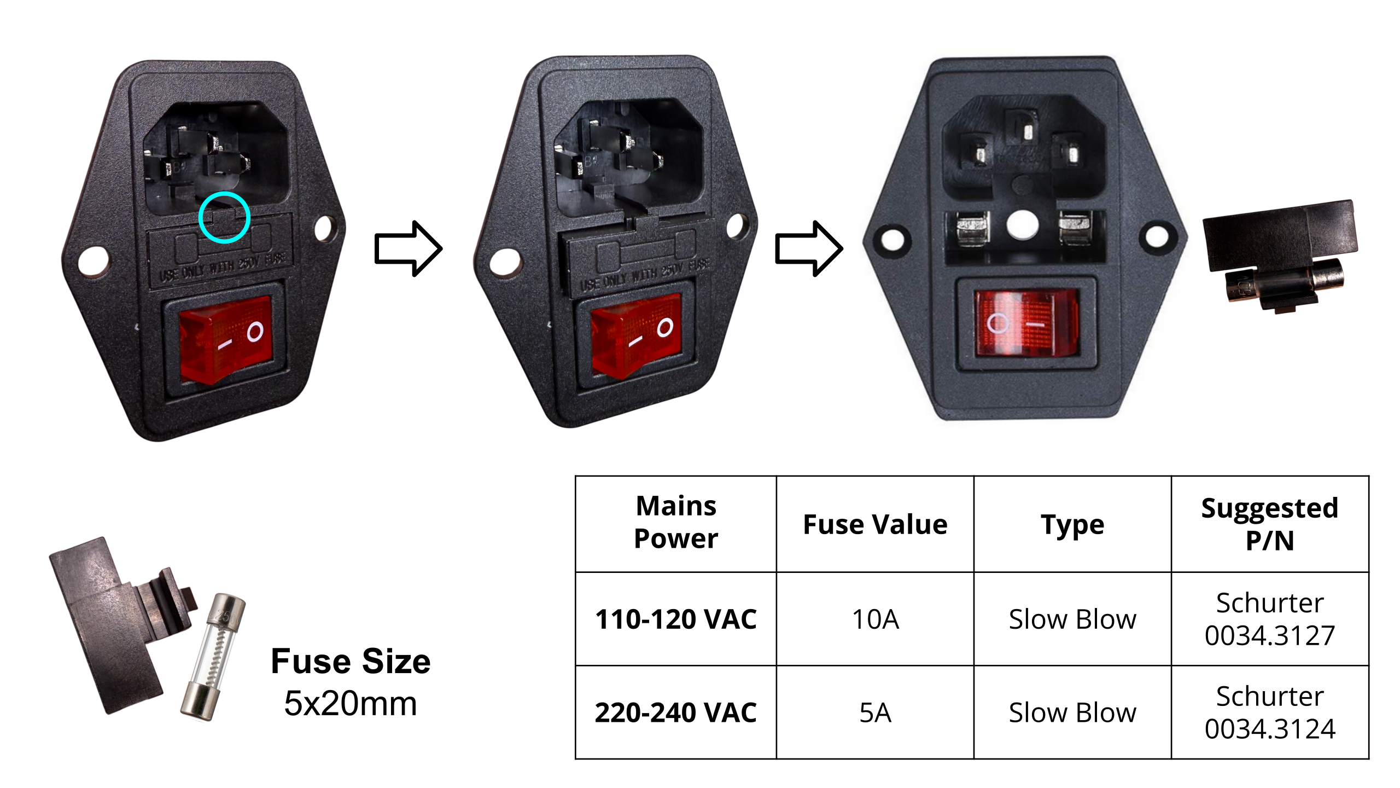
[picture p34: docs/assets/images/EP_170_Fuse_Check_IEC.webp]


### 8. Check Fuse Amperage - Bed Fuse (Z-07)

* This step is a safety check to make sure the components have the correct fuse sizes for your region.
* Remove the fuse and verify that the amperage rating matches the value listed in the table.
* Re-install the fuse

{: .warning }
Do not assume the installed fuses are correct. An oversized fuse may not blow when a fault occurs, which can allow wires or components to overheat. This can damage the printer, create a fire hazard, or cause serious injury. Always verify the fuse size before applying power.

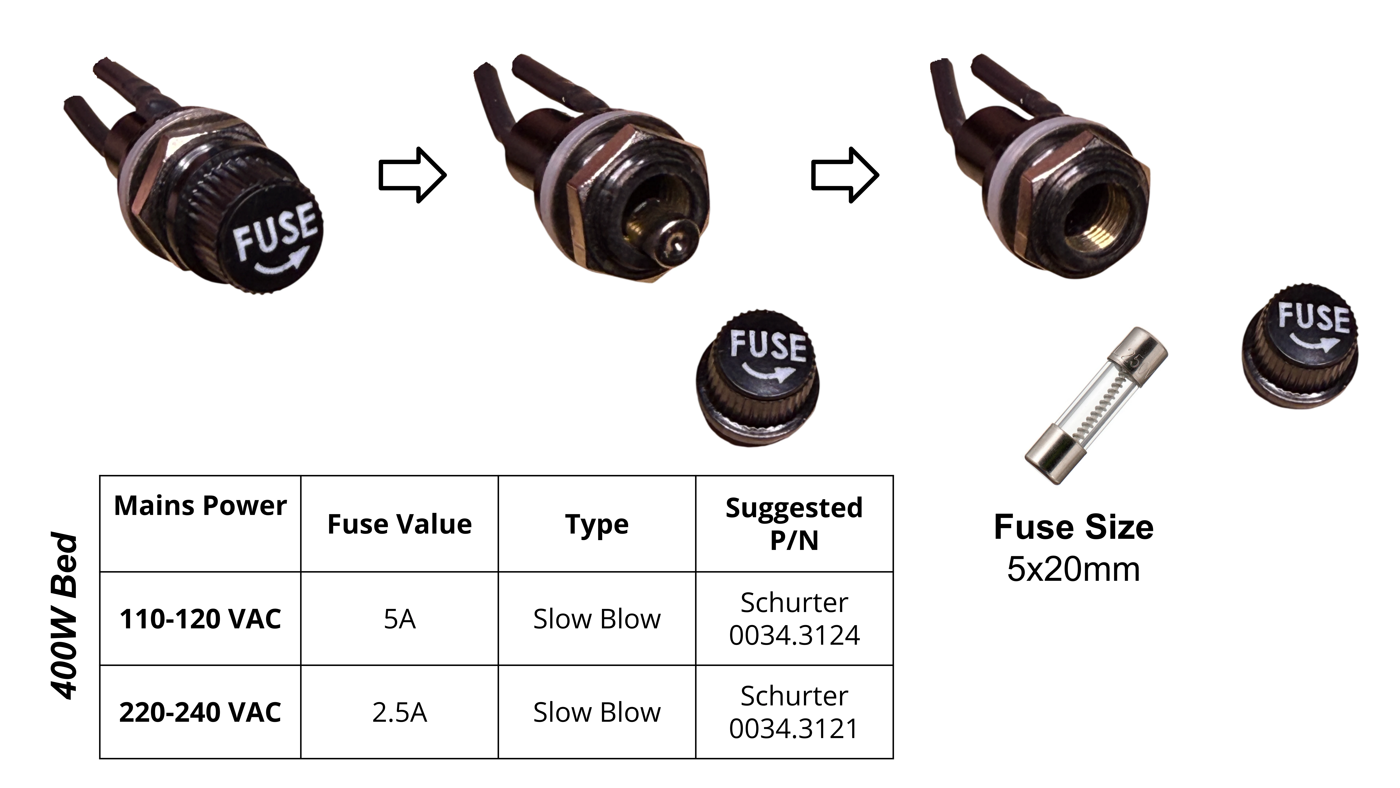
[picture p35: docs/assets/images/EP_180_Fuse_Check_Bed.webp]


### 9. Check PSU's AC Input Voltage Switch

* This step is a safety check to make sure the PSU is set to accept the mains power for your region.
* Locate the switch on the side of the PSU
* Ensure it is set to the AC input voltage for your region.

{: .warning }
Do not assume the PSU's AC input voltage switch is set correctly. An incorrectly set switch can damage the printer, create a fire hazard, or cause serious injury. Always verify the PSU's AC input voltage switch setting before applying power.

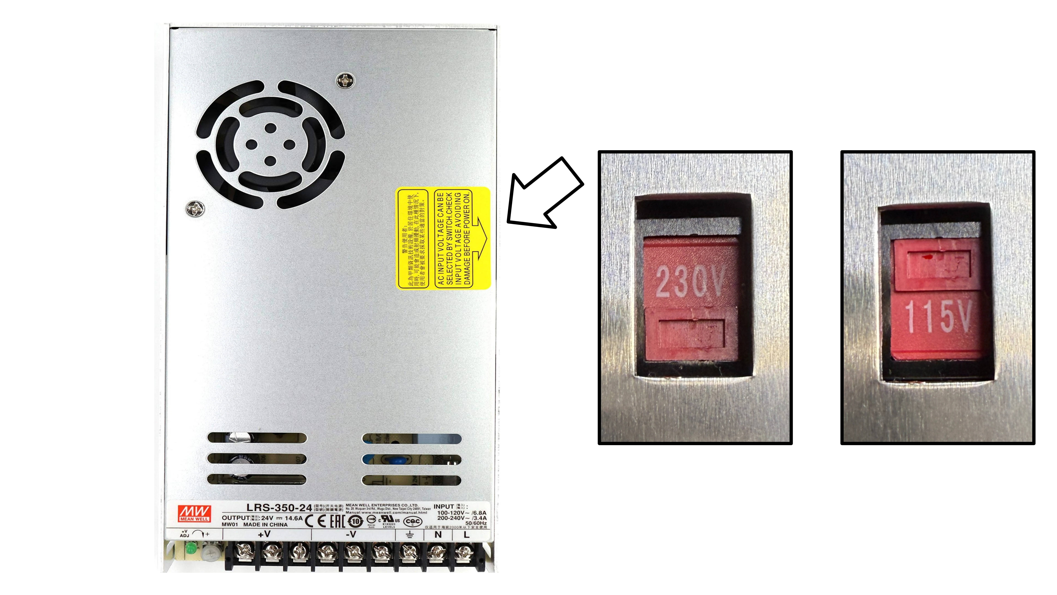
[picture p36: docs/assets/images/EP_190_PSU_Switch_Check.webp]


### 10. Install Cables: Z-01, Z-02, Z-03, Z-11, Z-12

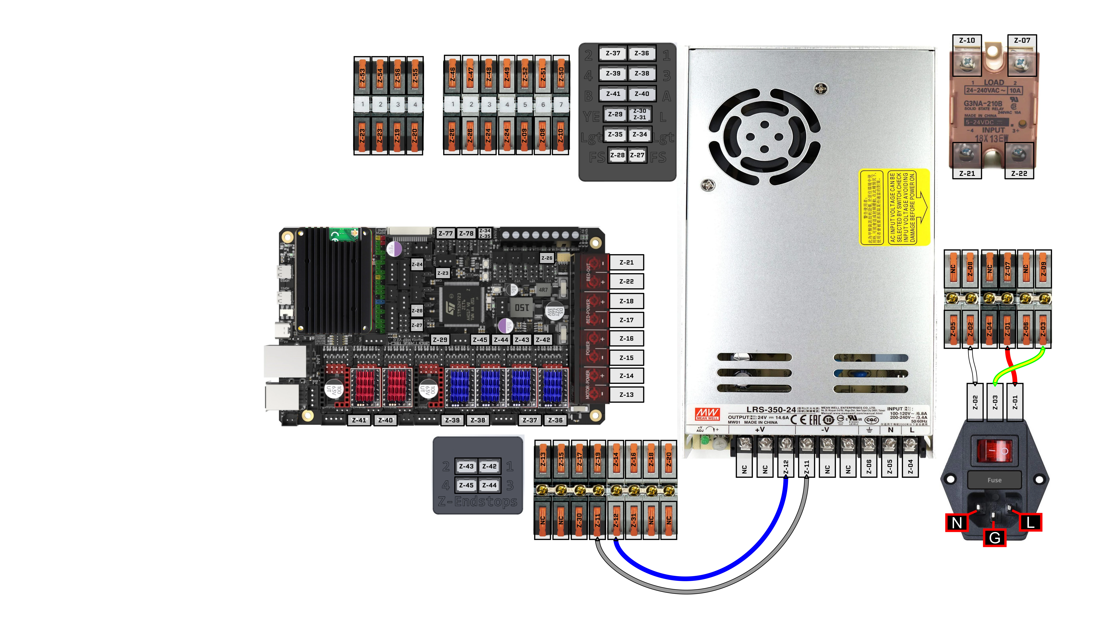
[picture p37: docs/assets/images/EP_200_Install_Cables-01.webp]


### 11. Install Cables: Z-04, Z-05, Z-06

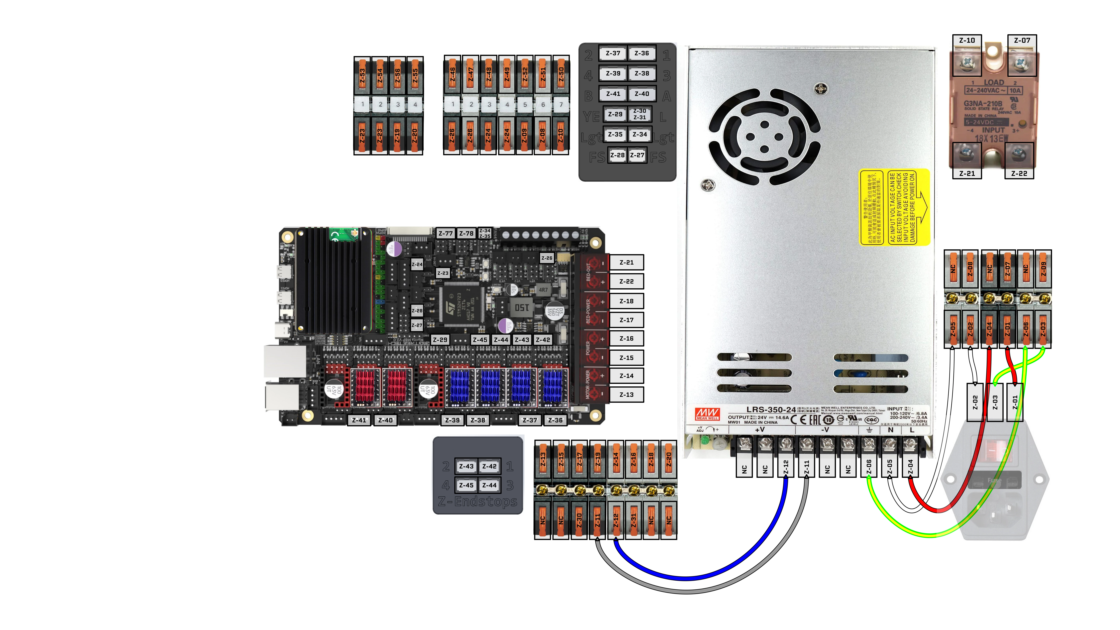
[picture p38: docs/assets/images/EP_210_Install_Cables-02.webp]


### 12. Prepare Multimeter for Continuity Checks

* Set multimeter to continuity mode
* Touch the multimeter leads together - The multimeter should beep

{: .note }
Always test the continuity mode is reporting accurately by touching the two multimeter leads together - This should result in a beeping noise.

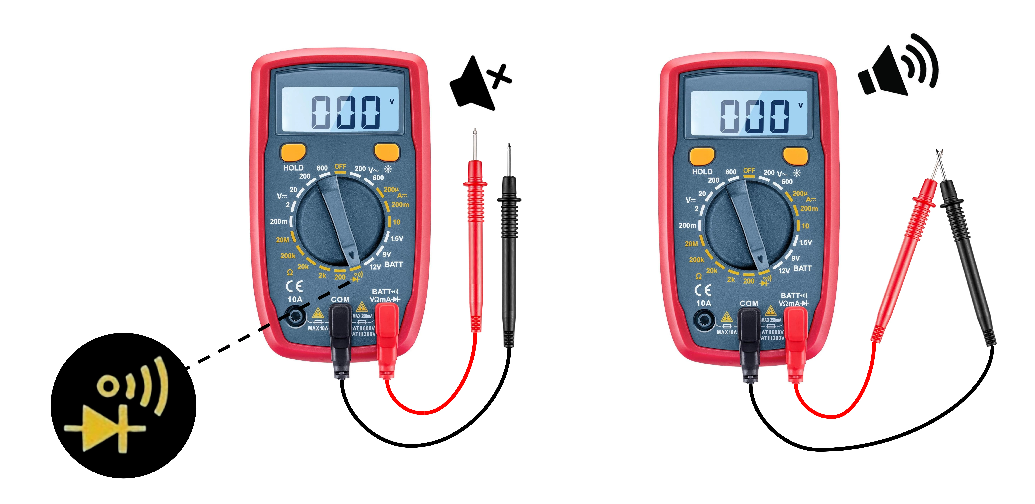
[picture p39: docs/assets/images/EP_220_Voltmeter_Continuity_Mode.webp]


<br>

### 13. Check for short between AC Live (L) and AC Neutral (N)

**Preprequisite:** 
* Power is disconnected
* Set multimeter to continuity mode
* Multimeter continuity mode tested and working (beeps when touching leads)

**Test:**
* Touch other lead to AC Live (L) bus bar
* Touch one lead to AC Neutral (N) bus bar

<span style="color:green">**Pass:** No Sound</span>

<span style="color:red">**Fail:** Multimeter Beeps</span>

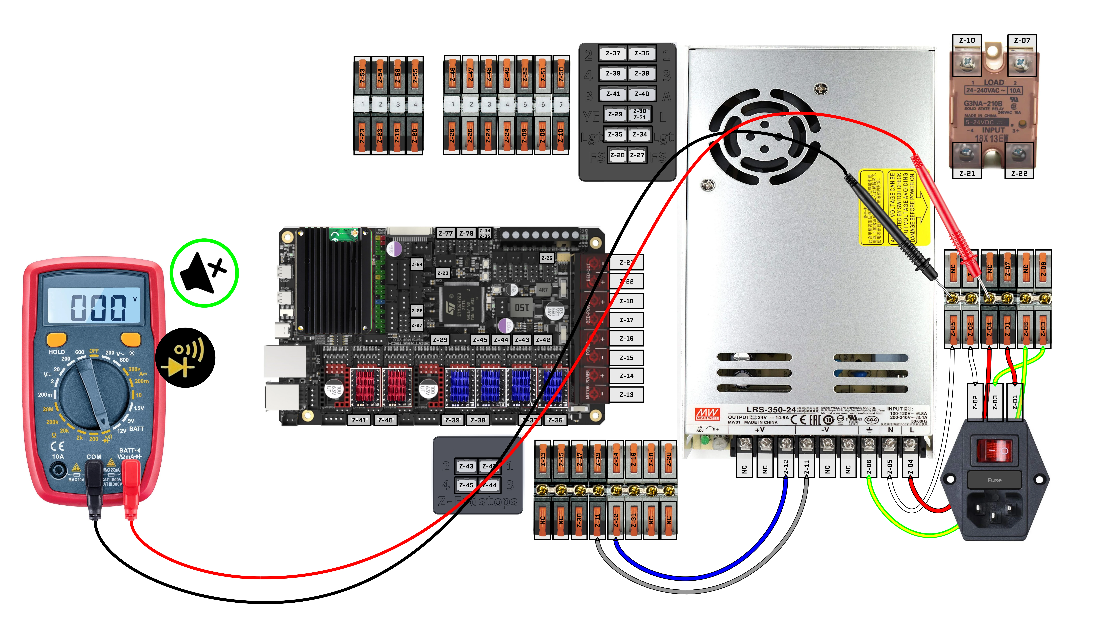
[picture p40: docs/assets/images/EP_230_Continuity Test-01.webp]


### 14. Check for short between AC Neutral (N) and AC Earth (⏚)

**Preprequisite:** 
* Power is disconnected
* Set multimeter to continuity mode
* Multimeter continuity mode tested and working (beeps when touching leads)

**Test:**
* Touch one lead to AC Neutral (N) bus bar
* Touch other lead to AC Earth (⏚) bus bar

<span style="color:green">**Pass:** No Sound</span>

<span style="color:red">**Fail:** Multimeter Beeps</span>

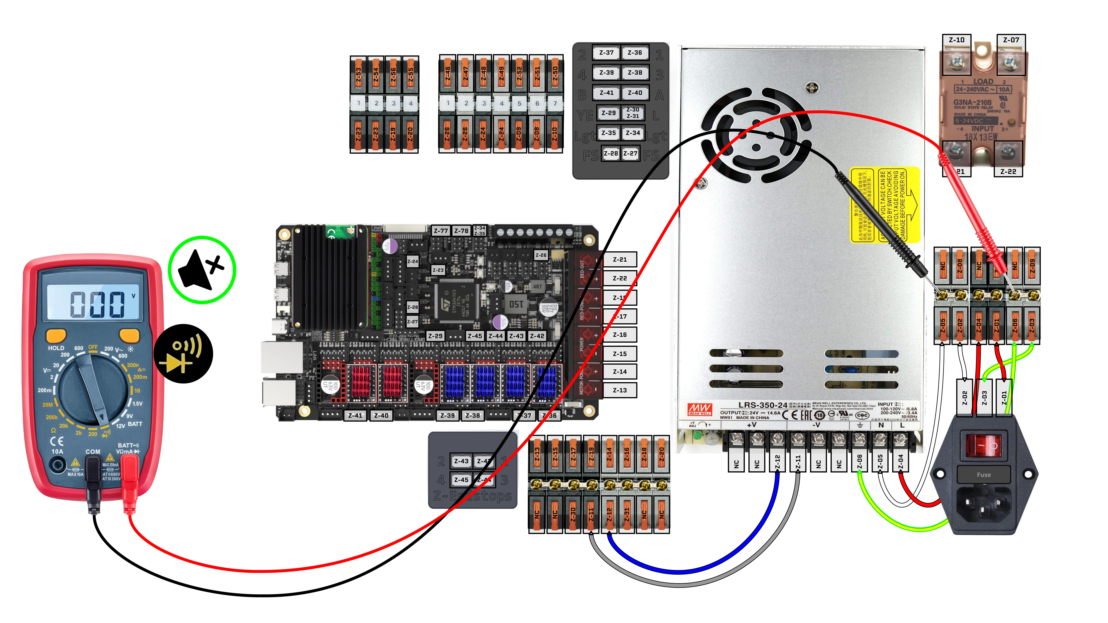
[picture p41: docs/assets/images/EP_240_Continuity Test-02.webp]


### 15. Check for short between AC Live (L) and AC Earth (⏚)

**Preprequisite:** 
* Power is disconnected
* Set multimeter to continuity mode
* Multimeter continuity mode tested and working (beeps when touching leads)

**Test:**
* Touch one lead to AC Live (L) bus bar
* Touch other lead to AC Earth (⏚) bus bar

<span style="color:green">**Pass:** No Sound</span>

<span style="color:red">**Fail:** Multimeter Beeps</span>

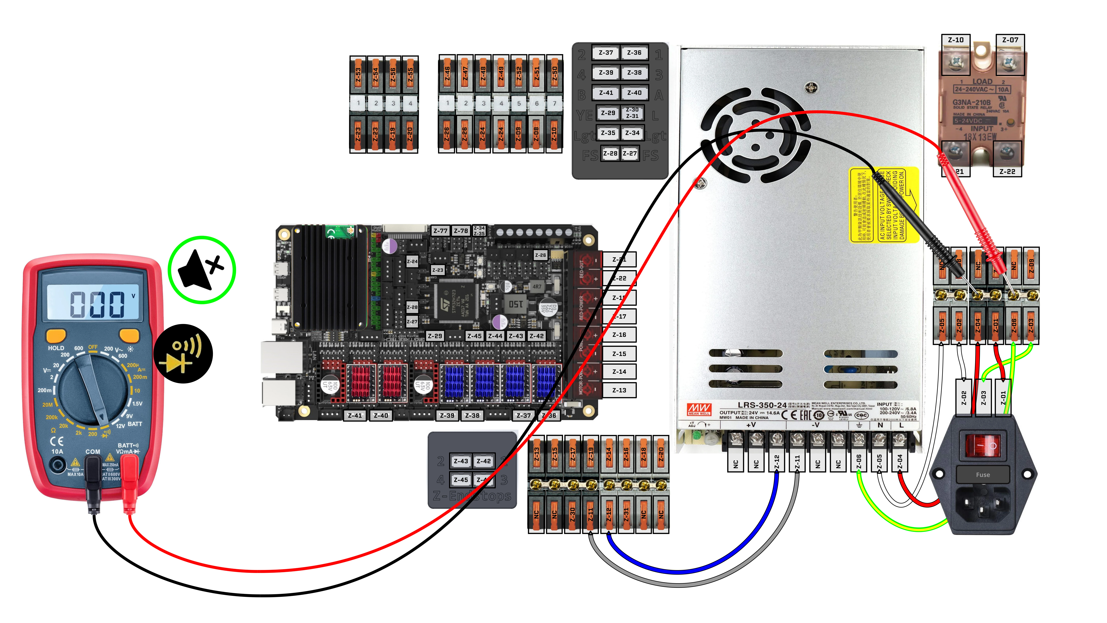
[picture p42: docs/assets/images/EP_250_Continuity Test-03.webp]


### 16. Check for short between PSU's DC(+) and DC(-)

**Preprequisite:** 
* Power is disconnected
* Set multimeter to continuity mode
* Multimeter continuity mode tested and working (beeps when touching leads)

**Test:**
* Touch one lead to DC(+) bus bar
* Touch other lead to DC(-) bus bar

<span style="color:green">**Pass:** No Sound</span>

<span style="color:red">**Fail:** Multimeter Beeps</span>

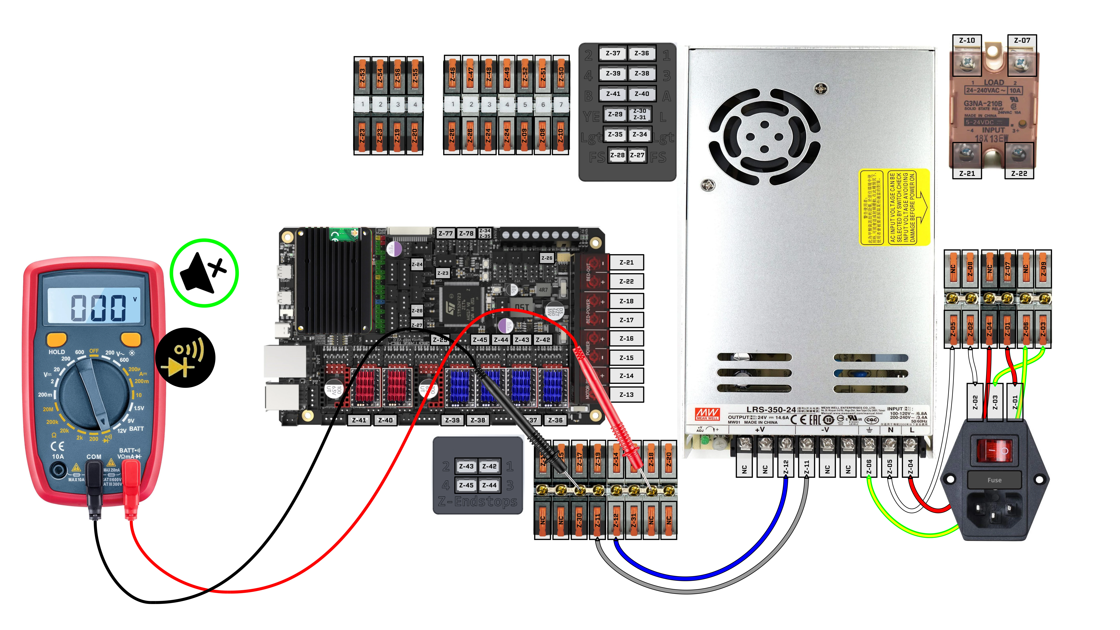
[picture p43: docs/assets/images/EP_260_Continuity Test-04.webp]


### 17. Check for continuity between IEC C14 plug and PSU for AC Live (L)

**Preprequisite:** 
* Power is disconnected
* Set multimeter to continuity mode
* Multimeter continuity mode tested and working (beeps when touching leads)

**Test:**
* Touch one lead to IEC C14 Plug's (L) pin
* Touch other lead to PSU's AC (L) input

<span style="color:green">**Pass:** Multimeter Beeps</span>

<span style="color:red">**Fail:** No Sound</span>

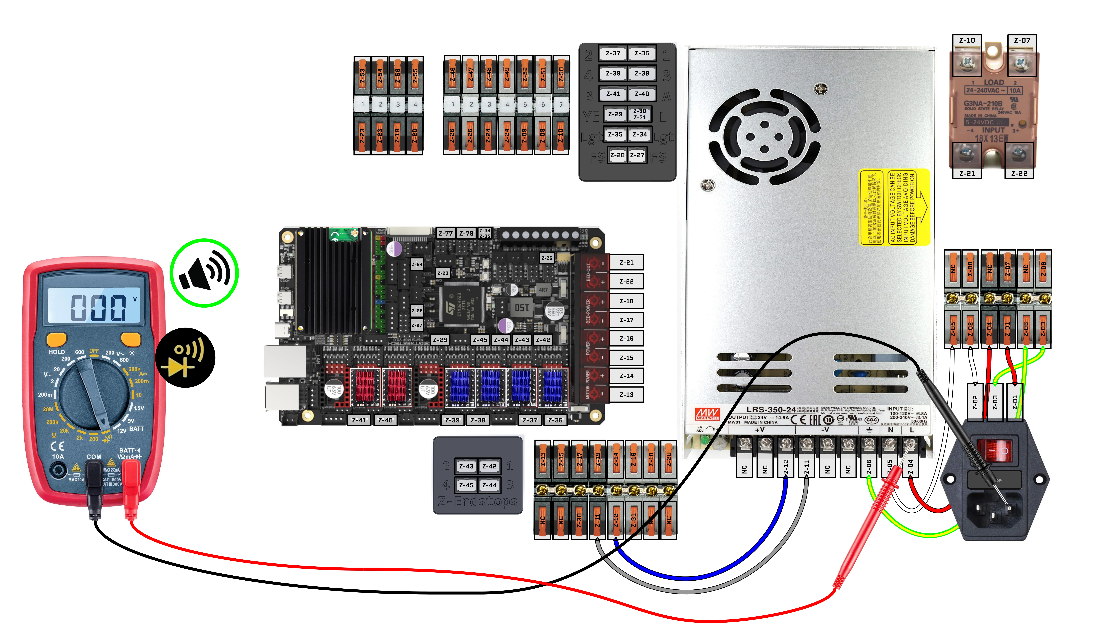
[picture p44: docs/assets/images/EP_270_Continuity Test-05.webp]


### 18. Check for continuity between IEC C14 plug and PSU for AC Neutral (N)

**Preprequisite:** 
* Power is disconnected
* Set multimeter to continuity mode
* Multimeter continuity mode tested and working (beeps when touching leads)

**Test:**
* Touch one lead to IEC C14 Plug's (N) pin
* Touch other lead to PSU's AC (N) input

<span style="color:green">**Pass:** Multimeter Beeps</span>

<span style="color:red">**Fail:** No Sound</span>

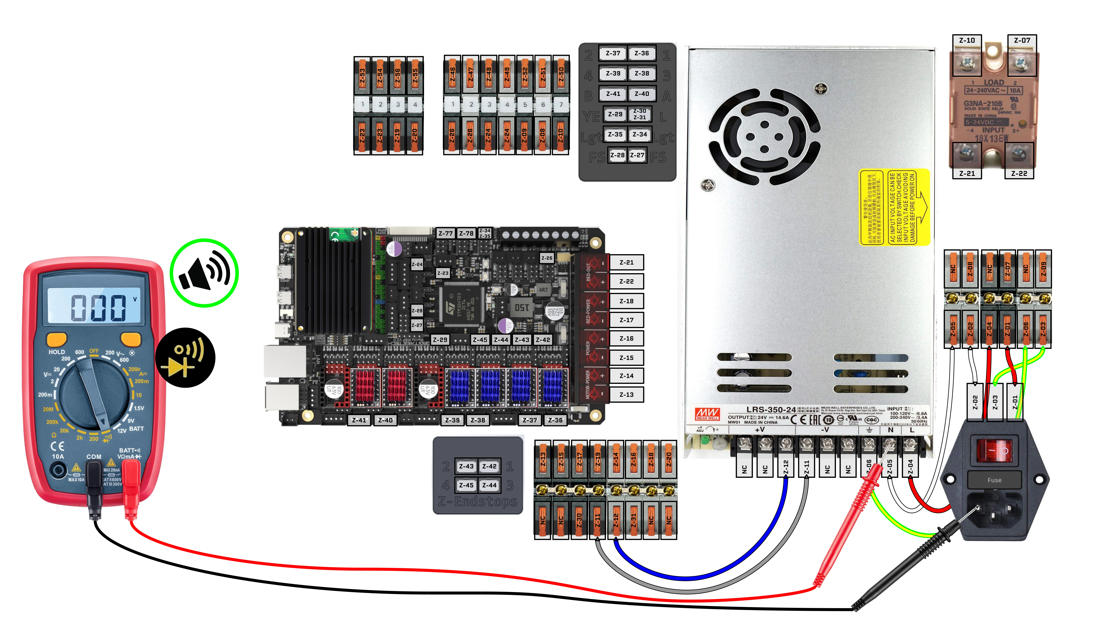
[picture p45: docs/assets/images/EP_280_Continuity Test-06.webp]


### 19. Check for continuity between IEC C14 plug and PSU for AC Earth (⏚)

**Preprequisite:** 
* Power is disconnected
* Set multimeter to continuity mode
* Multimeter continuity mode tested and working (beeps when touching leads)

**Test:**
* Touch one lead to IEC C14 Plug's (⏚) pin
* Touch other lead to PSU's AC (⏚) input

<span style="color:green">**Pass:** Multimeter Beeps</span>

<span style="color:red">**Fail:** No Sound</span>

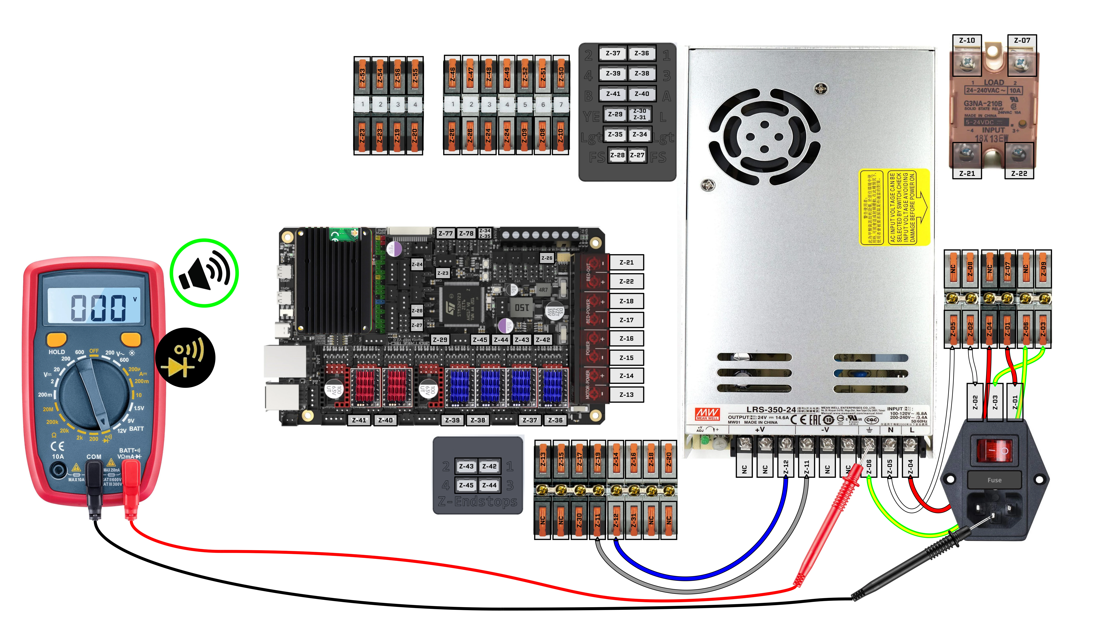
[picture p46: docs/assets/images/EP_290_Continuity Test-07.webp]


### 20. Preparing for First Power ON

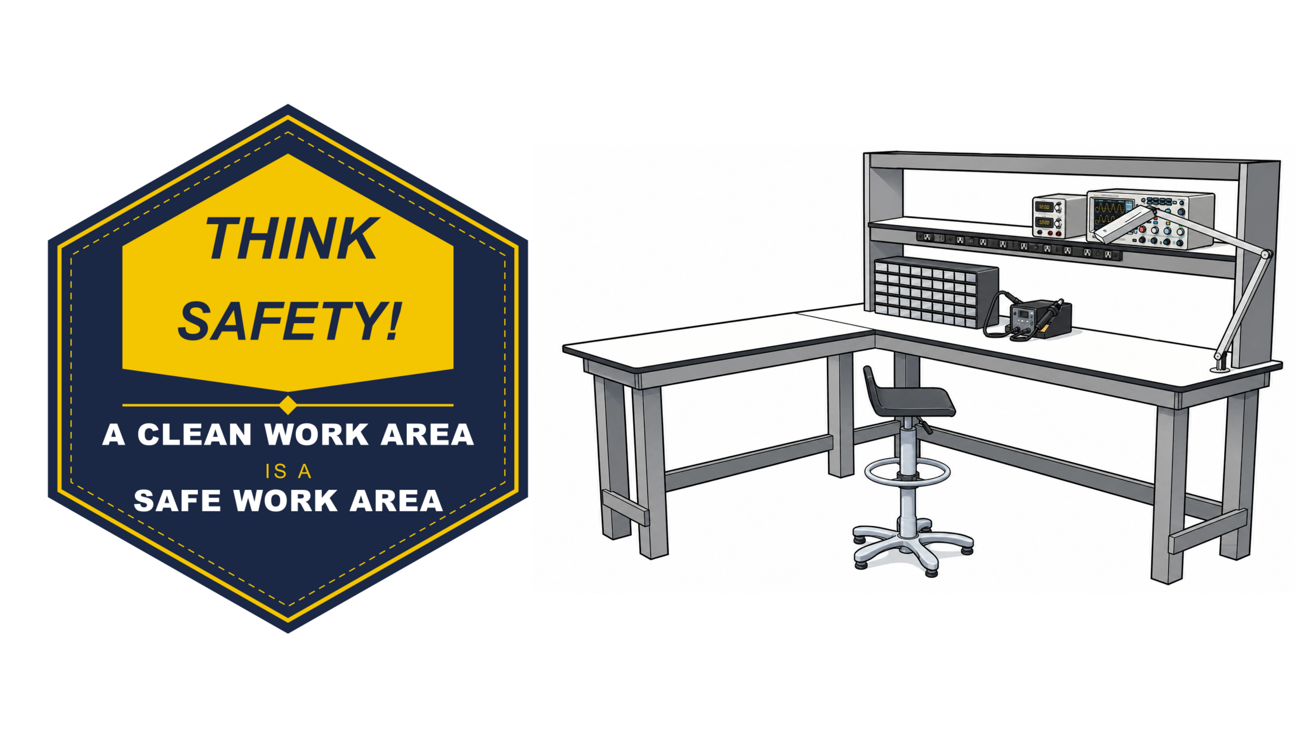
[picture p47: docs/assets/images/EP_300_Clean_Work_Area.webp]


{: .warning }
Don’t wire electronics in a cluttered area, as it greatly increases the risk of accidentally shorting something.

### Always prioritize your safety and the safety of those around you
* Wear safety glasses, and make sure anyone observing nearby does the same.
* Anyone working close enough to accidentally contact electrical components should wear insulating gloves.
* Be prepared. The odds may be low, but they are not zero. Keep a fire extinguisher nearby in case of faulty components or a wiring mistake.

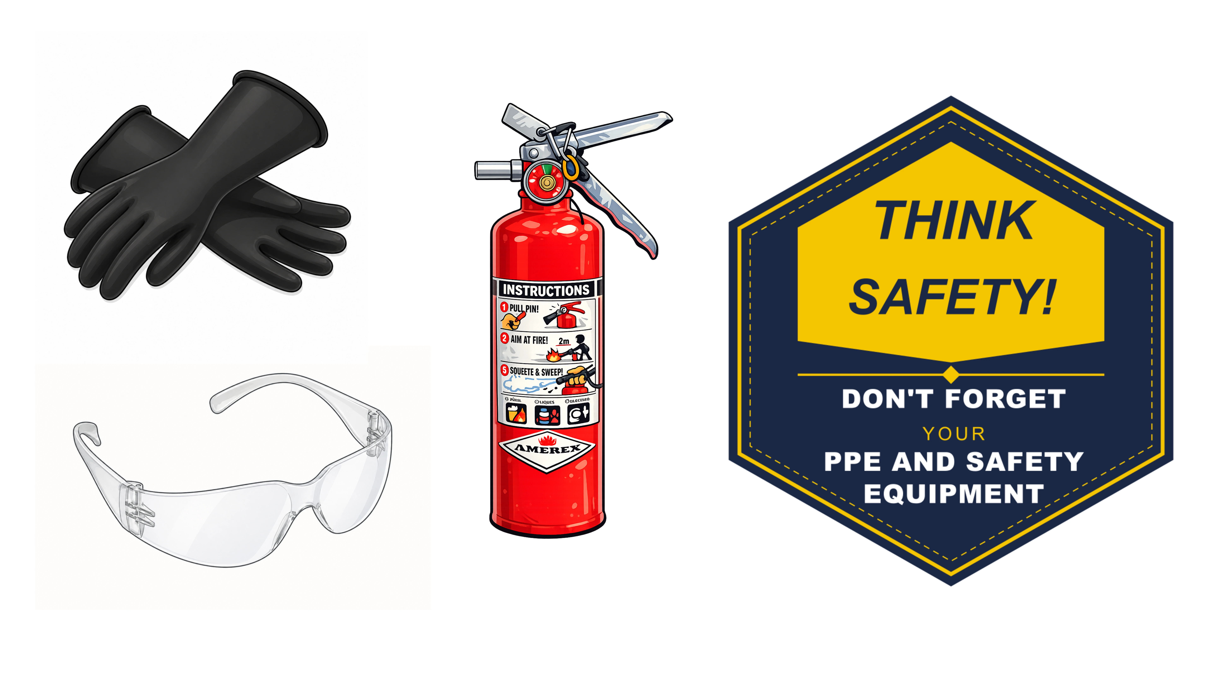
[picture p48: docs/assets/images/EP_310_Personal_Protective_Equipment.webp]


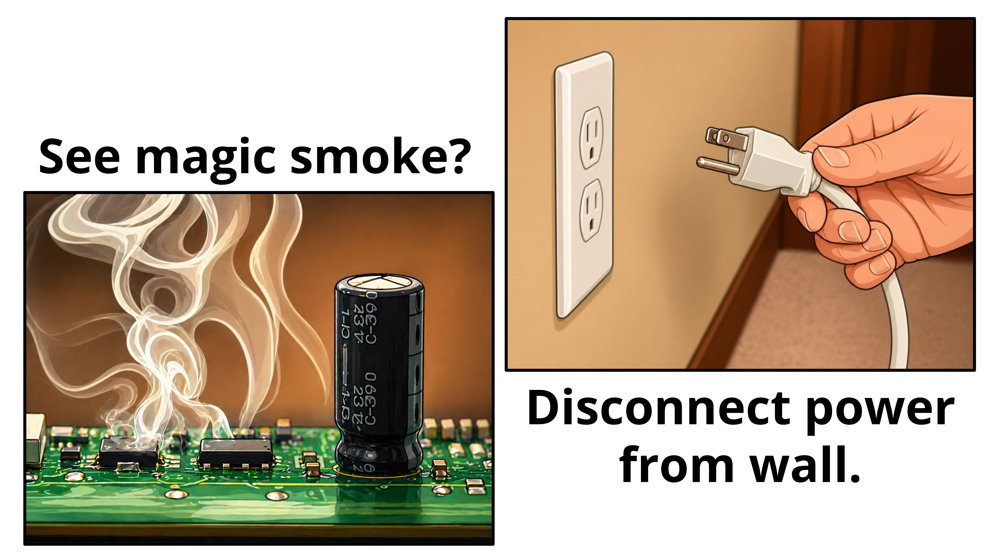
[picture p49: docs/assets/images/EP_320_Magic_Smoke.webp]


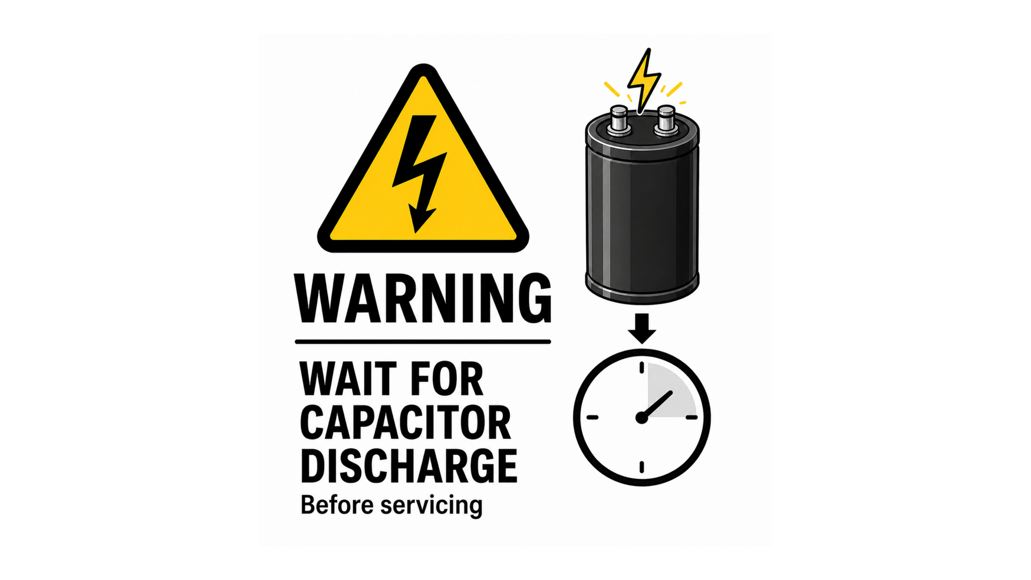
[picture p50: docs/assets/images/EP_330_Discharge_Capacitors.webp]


{: .important}
In the following steps, the power supply unit (PSU) will be turned on. After the PSU is turned off, wait several minutes before handling any electronics to allow the capacitors to fully discharge.

### 21. Adjusting PSU to 24V

Now that you are working safe and responsibly, lets get on with it!

**Prerequisite:** Power is disconnected, jumpers installed, PSU power switch checked, fuses checked, continuity checks all passed

1. **Safety First:** Ensure you and others around you observing are wearing the appropriate PPE. Also have your safety equipment on hand.
2. Set voltmeter to DC Voltage Mode, choosing the lowest limit that is >=24V. In our image, that number is 200.
3. Connect the voltmeter's leads to the corresponding polarity terminals on the 24V lift lever terminal block: red lead to V+ and black lead to V−.
4. Connect power cable, hold on to your butts, and power ON. A LED should light up on 24V PSU. Voltmeter should now have a reading close to 24V.
5. Adjust the potentiometer on the 24V PSU until voltmeter reads 24V.
6. Power OFF and disconnect the power cable. Remove the voltmeter from the 24V terminal block.

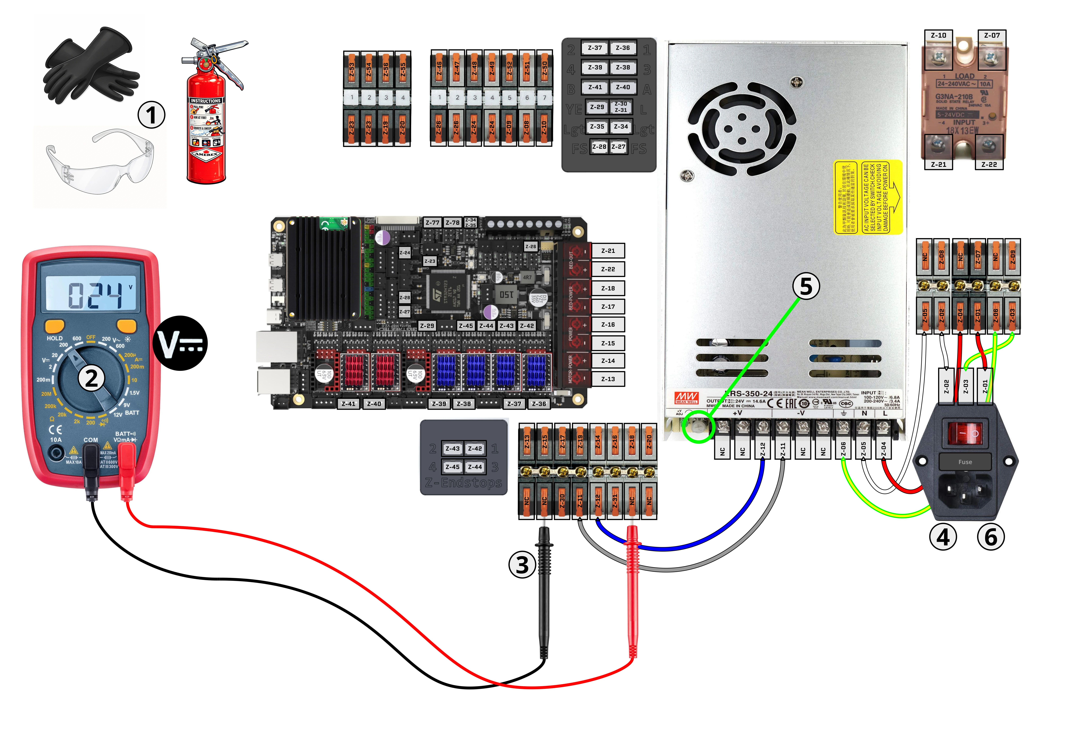
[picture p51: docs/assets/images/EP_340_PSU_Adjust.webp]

<!-- ![]({{site.url}}/{{site.baseurl}}/assets/images/EP_340_PSU_Adjust.webp) -->

### 22. Install Terminal Block Covers

* Install terminal block covers for Terminal Block AC Power (TBAC) and Terminal Block DC Power (TBDC)

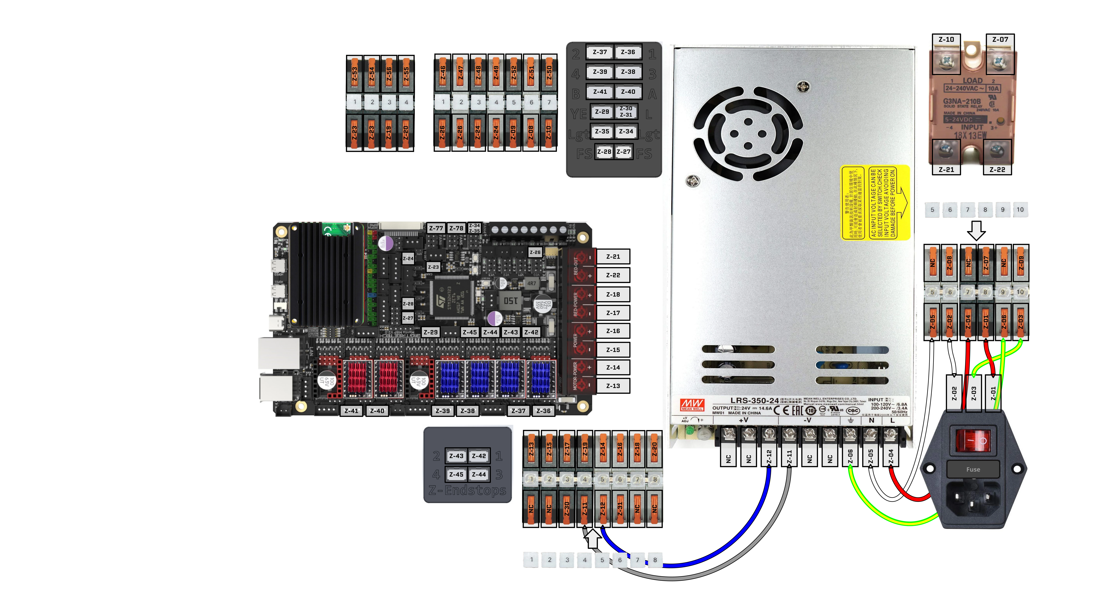
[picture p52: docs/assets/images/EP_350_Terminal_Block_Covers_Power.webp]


### 23. Install Cables: Z-13, Z-15, Z-17, Z-19

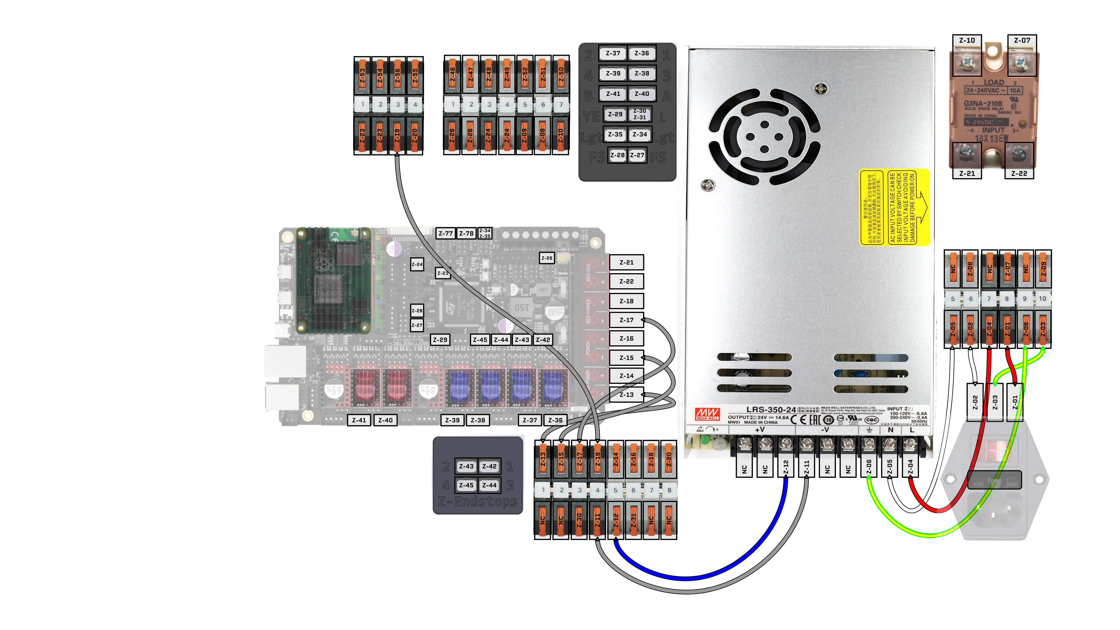
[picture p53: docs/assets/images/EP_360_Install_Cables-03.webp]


### 24. Install Cables: Z-14, Z-16, Z-18, Z-20

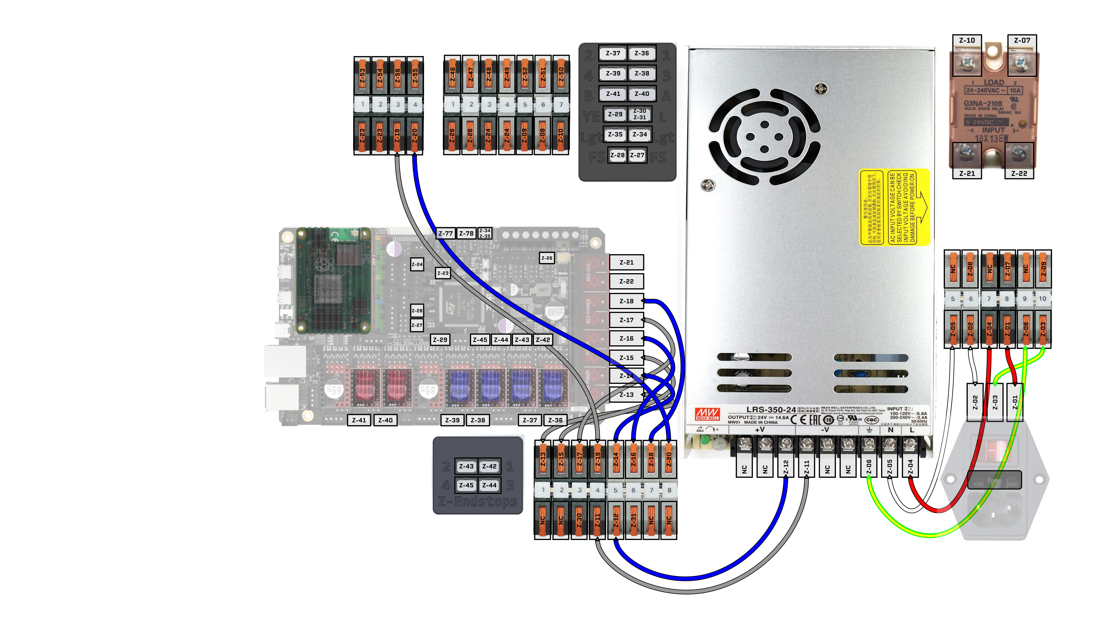
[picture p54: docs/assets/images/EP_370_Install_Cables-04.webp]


### 25. Install Cables: Z-07, Z-08, Z-09, Z-10, Z-21, Z-22

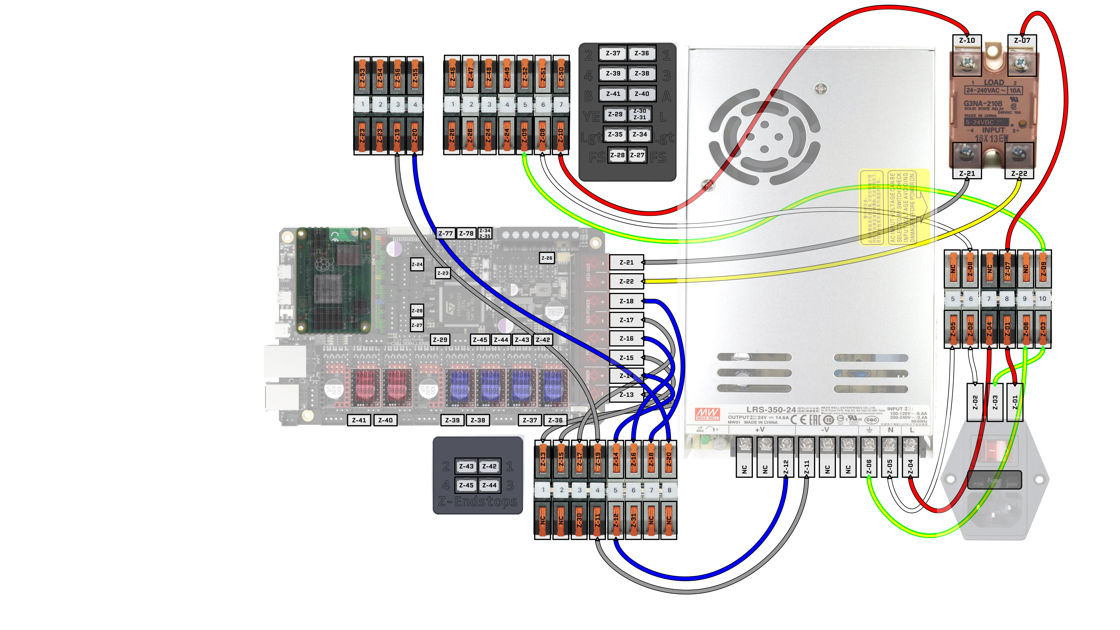
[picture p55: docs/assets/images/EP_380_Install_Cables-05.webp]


### 26. Install Cables: Z-23, Z-24, Z-26

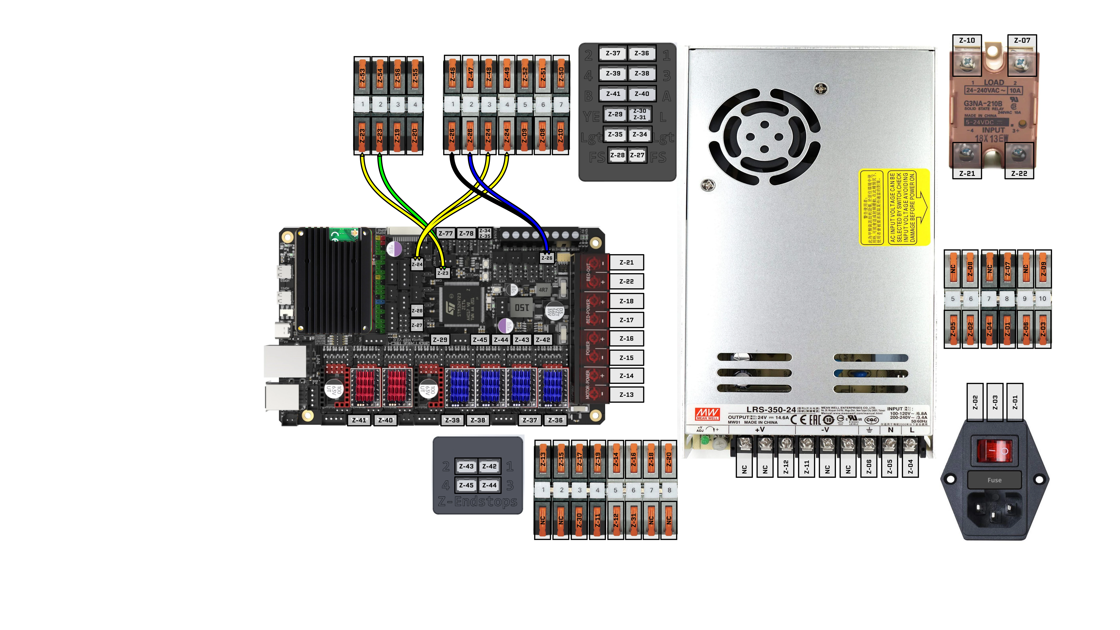
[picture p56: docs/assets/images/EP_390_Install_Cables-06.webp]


### 27. Assembling Peripheral Blocks

* Feed cables through peripheral block
* Connector should be held snug by peripheral block when pushed into place.
  * Evauluate the fit
    * **Too Tight:** stop and reprint - scale part larger
    * **Good Fit:** Part snaps into place and is secure (doesn't pop out)
    * **Too Loose:** Dab of hot glue on back or Reprint - Scale part smaller
* Optional: Apply labels or indicators at connector.
* Apply zip-ties

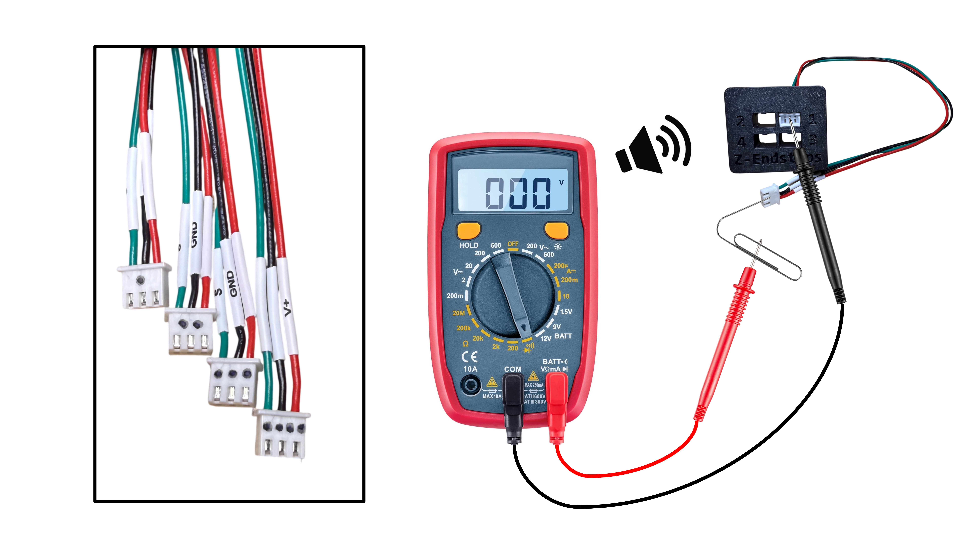
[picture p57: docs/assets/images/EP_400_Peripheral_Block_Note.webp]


{: .note}
Before zip typing cables in next steps, you can add indicators or simply the Z-codes on the connector with sharpie. Otherwise, the cables can be identified using a continuity test as they are connected to the main board in later steps - Hold off plugging them in for now! A paperclip provides good access for the female connectors.

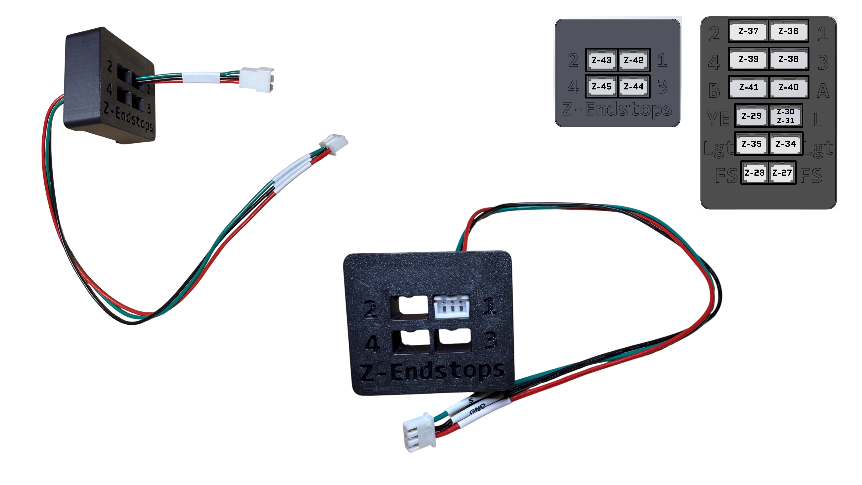
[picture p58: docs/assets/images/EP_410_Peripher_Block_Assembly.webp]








### 28. Install Cables: Z-42, Z-43, Z-44, Z-45



### 29. Install Cables: Z-27, Z-28



### 30. Install Cables: Z-34, Z-35, Z-32/33



### 31. Install Cables: Z-29, Z-30, Z-31



### 32. Install Cables: Z-40, Z-41



### 33. Install Cables: Z-38, Z-39



### 34. Install Cables: Z-36, Z-37



### 35. Complete the [Electronics Backpack]({{site.url}}/{{site.baseurl}}/doc_tree/2_assembly/14_electronics_backpack/0_electronics_backpack.html#animated-assembly) Section then Continue



<!-- ![]({{site.url}}/{{site.baseurl}}/assets/images/EP_520_Continue_Youtube_Electronics_Backpack.webp) -->

<br>

### 36. Install Cables: Z-25, Z-48, Z-49, Z-53, Z-54, Z-55, Z-56, Z-60, Z-61, Z-114



### 37. Unplug Toolhead's XT30 Connector



### 38. Checking Toolhead Power

* **Safety First:** Ensure you and others around you observing are wearing the appropriate PPE. Also have your safety equipment on hand
* Ensure the toolhead is unplugged
* Set voltmeter to DC Voltage Mode, choosing the lowest limit that is >=24V. In our image, that number is 200
* Power ON the printer
* Touch the voltmeter's leads to the XT30 connector as shown - **Approach from the outside as to not cause an accidental short**
  * Black to Black
  * Red to Blue
* The voltmeter should read a positive 24V
* Power OFF the printer

<span style="color:green">**Pass:** Voltmeter reads **positive +24V**</span>

<span style="color:red">**Fail:** Voltmeter reads **negative -24V**, or any other value</span>

{: .warning }
Polarity matters! Make sure you are touching the correct leads to the correct points. This is the last safety check to save your toolhead board.



### 39. PZ Probe Controller Cable: Z-105, Z-106, Z-107

* This cable needs a little extra explanation.
  * Z-105 and Z-106 are used to program trigger variables outside of E3D’s preset options. These connectors are not required for normal operation and can either be tucked behind the toolhead board for later use or removed.
  * Z-107 provides power to the PZ Probe Controller and carries the trigger signal.
* Verify Z-107 pinout on both ends of the connector and make sure power, ground, and signal are routed correctly



{: .warning }
The PZ Probe Controller is fragile and can be damaged if Z-107 is wired incorrectly.

### 40. Install Lights, Endstops, Electronics Fans, Camera: Z-57, Z-58, Z-59, Z-68, Z-69, Z-70, Z-71, Z-72, Z-77, Z-78, Z-116



### 41. Endstop Check

* This step checks the Z-endstop wiring at the board connection to confirm the wiring is correct.
* Unplug and test one endstop at a time so each connector can be easily returned to its original location after testing.
* Paperclips can be used to make it easier to access the female pins during the check.

**Preprequisite:** 
* Power is disconnected
* Set multimeter to continuity mode
* Multimeter continuity mode tested and working (beeps when touching leads)

**Test:**
* Unplug endstop cable from the board connection.
* If needed, insert paperclips into the V+ and Signal lines of the endstop cable as shown.
* Touch multimeter leads to paperclips.
* Plug endstop cable back into the board.

<span style="color:green">**Pass:** Multimeter beeps when the switch is not pressed; no sound when the switch is pressed.</span>

<span style="color:red">**Fail:** Any other behavior</span>





{: .warning }
Incorrect endstop wiring could short power to ground, so this check is important!

### 42. Electronics Fans Pinout Check: Z-77, Z-78

* Check that the electronic fan pinout is wired as shown.



{: .warning }
The electronic fan pinout on the first batch of kits was commonly reported NOK, so please check it before proceeding.

### 43. Install Bed Heater, Bed Fans: Z-46, Z-47, Z-50, Z-51, Z-52



### 44. Install Stepper Motors: Z-46, Z-47, Z-50, Z-51, Z-52



## Continue to the [Firmware Guide]({{site.url}}/{{site.baseurl}}\doc_tree\4_firmware\firmware.html)

This concludes the electronics backpack wiring required for firmware installation. We will integrate the remaining components in later steps.

{: .warning }
At this stage, only the cables that we have covered should be connected.

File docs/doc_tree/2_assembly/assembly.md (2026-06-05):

---
title: Assembly Guide
layout: assembly
nav_order: 2
---
# Assembly Guide

## How To Use This Guide

{: .warning }
This ain't a toaster. It's much more dangerouser. You can hurt yourself or your cat. Please do not attempt to build unless you are confident you have the skills, tools, time, and patience. A warning like this will show up where extra care should be taken.

{: .important }
If you are building this printer for the first time, it is highly recommended that you go through this entire documentation page, in order.

{: .note }
Sometimes there's a note.

## Materials
### A table like this will display hardware, printed parts, and tools needed for the sub-assembly

| Hardware | Qty |
|:---|:----|
| M3x25 SHCS | 5 |
| GT2 Timing Pulley, 20T, 6mm Belt, 5mm ID| 1 |
| *Video Name (Bag Name) | 2 |
| Tabby Cat | 100 |

***Whats in a name?** It's a large BOM and a long documentation process. Name preferences were occasionally mixed up along the way. We will try to have the bag label name in parenthesis next to the video callout name where they differ.

## Tools
### Essential
 - Standard Metric Hex Key Set, Ball-End, 1.5-10mm
 - Long Handle Hex Key, 3mm
 - Soldering Iron
 - Small/Mini Pliers or Adjustable Wrench
 - Cyanoacrylate Gel, i.e. Loctite Prism 454 or Gorilla Super Glue Gel
 - Flush Cutters
 - Phillips Screwdriver, #2
 - Pen Knife / X-Acto Knife / Razor Blade

### Optional, But Really Helpful
 - SciGrip #16 Acrylic Cement
 - Blue "medium strength" Loctite
 - Boron Nitride Paste
 - Arbor Press
 - Machinist's Square
 - Dial Guage/Indicaator and Precision 1-2-3 Block

## Interactive Views
### You'll also see 3d views like this one. 
 - Rotate with left-click (or one finger on mobile)
 - Pan with right-click (two fingers on mobile)
 - Zoom with scroll wheel (pinch on mobile)
 - Refresh the page to recenter the model

## General Guidelines
 - It is recommended to use Blue Loctite on all metal-metal threads that you wouldn't expect to service regularly.
 - Cyanoacrylate Gel can generally be applied to screws when threading into plastic. 
 - We try to note where exceptions occur, but it's always good to practice common sense or see "Issues" below.
 - When threading into plastic, only tighten until the head makes contact, these connections are not meant to provide clamping force.
 - It will be easiest to follow if printed parts are organized by assembly according to the folder structure on the GitHub.
 - It can be helpful to organize screws and nuts by type and size beforehand.

## YouTube Playlist

{: .note}
>- It's a good idea to watch through each video before assembly just to get an idea of what's needed, when tools appear, sequence, etc. Then go back and follow along while building. 
>- The playlist below is here for convenience, but it's better to navigate the build via the sidebar on the left.

<iframe style='width:100%; height:621px;' src="https://www.youtube.com/embed/BFysg58AneA?si=BnFOLAoJyxAxuOTr](https://www.youtube.com/embed/videoseries?si=k8YJyXBpN_D6w89W&amp;list=PL98gg-9q2S-WK1jO8WXkpYlPxK7jg6Ywa" title="YouTube video player" frameborder="0" allow="accelerometer; autoplay; clipboard-write; encrypted-media; gyroscope; picture-in-picture; web-share" referrerpolicy="strict-origin-when-cross-origin" allowfullscreen></iframe>

<!-- <iframe width="560" height="315" src="https://www.youtube.com/embed/videoseries?si=k8YJyXBpN_D6w89W&amp;list=PL98gg-9q2S-WK1jO8WXkpYlPxK7jg6Ywa" title="YouTube video player" frameborder="0" allow="accelerometer; autoplay; clipboard-write; encrypted-media; gyroscope; picture-in-picture; web-share" referrerpolicy="strict-origin-when-cross-origin" allowfullscreen></iframe> -->

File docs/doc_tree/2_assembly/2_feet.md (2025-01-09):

---
title: Feet
layout: assembly
parent: Assembly Guide
nav_order: 2
---

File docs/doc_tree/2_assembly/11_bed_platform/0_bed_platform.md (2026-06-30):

---
title: Bed Platform
layout: assembly
parent: Assembly Guide
nav_order: 11
---

# Bed Platform



{: .note}
All the modules from this section are presented in one video.

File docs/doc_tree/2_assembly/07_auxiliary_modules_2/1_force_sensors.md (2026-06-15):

---
title: Force Sensors
layout: assembly
parent: Auxiliary Modules Pt. 2
nav_order: 1
---

# Force Sensors


## Materials

| Hardware (for each sensor) | Qty | 
|:---|:----|
| WAGO Connector - 2-Pin | 2 |
| M5x20 Dowel Pin | 2 |
| Die Spring | 1 |
| Magnet Cube | 1 |
| Magnet 6mm x 3mm | 2 |
| Makerbeam XL T-Nut | 1 |
| M3x45 SHCS (Stainless) | 1 |
| M3x5.7 Brass Insert | 1 |
| M3x12x1 Oversized Washer | 2 |
| M3x7x0.5 Washer | 5 |
| M4x12x1 Washer | 2 |
| M4x12x1 Nylon Washer | 2 |
| Wave Spring Washer | 2 |
| M3 Nyloc Nut | 2 |
| M3 Cap Nut (Acorn Nut) | 1 |
| PTFE Tube - 3mm ID x 4mm OD (cut from long piece)  | 10mm|

| Cables - Side A                      | 
|:-------------------------------------|
| Z-60                                 |
| Z-73                                 |
| Z-74                                 |
| **Cables - Side B**                  | 
| Z-61                                 |
| Z-75                                 |
| Z-76                                 |

| Printed Parts | Qty |
|:---|:----|
| <a href="https://github.com/AutomatedLayers/VertigoMk1/blob/main/hardware/STL/10%20Auxilliary%20Modules%20%26%20Cable%20Routing/Force%20Triggers/Force%20Sensor%20Frame%20Moun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" target="_blank">Force Sensor Frame Mount A</a> | 1  |
| <a href="https://github.com/AutomatedLayers/VertigoMk1/blob/main/hardware/STL/10%20Auxilliary%20Modules%20%26%20Cable%20Routing/Force%20Triggers/Force%20Sensor%20Frame%20Moun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" target="_blank">Force Sensor Frame Mount B</a> | 1  |
| <a href="https://github.com/AutomatedLayers/VertigoMk1/blob/main/hardware/STL/10%20Auxilliary%20Modules%20%26%20Cable%20Routing/Force%20Triggers/Force%20Sensor%20Plug%20-%20Q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" target="_blank">Force Sensor Plug</a> | 2  |
| <a href="https://github.com/AutomatedLayers/VertigoMk1/blob/main/hardware/STL/10%20Auxilliary%20Modules%20%26%20Cable%20Routing/Force%20Triggers/Force%20Sensor%20Rocker%20-%2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" target="_blank">Force Sensor Rocker</a> | 2  |
| <a href="https://github.com/AutomatedLayers/VertigoMk1/blob/main/hardware/STL/00%20Tools/Force%20Sensor%20Washer%20Setting%20Tool.stl" target="_blank">Force Sensor Washer Setting Tool</a> | 1  |

## Animated Assembly

<iframe style='width:100%; height:621px;' src="https://www.youtube.com/embed/C0KE_nT1YOo?si=bt00TVDFhj8J_SiP" title="YouTube video player" frameborder="0" allow="accelerometer; autoplay; clipboard-write; encrypted-media; gyroscope; picture-in-picture; web-share" referrerpolicy="strict-origin-when-cross-origin" allowfullscreen></iframe>

## Assembly Notes

 - **0:29** See the magnet polarity information below. We will make sure the magnets in the Bed Scraper Bar attract to the Force Sensors when we get to that section.
 - **0:41** These two magnets are a just a low profile way of retaining the more powerful cube magnet just installed.
 - **1:54** Compression of wave spring washers is not to scale.
 - **2:13** The PTFE will need to be cut from the long section of 3mm ID tube in the kit.
 - **2:19** You may need to hold the PTFE (gently with pliers if necessary) and screw the M3 into it if it doesn't slide on.
 - **2:40** The gap here is just to see that the PTFE stays up against the M3 washer on the left when the brass insert is threadlocked in place.
 - **2:46** Threadlocker or glue of your choice will work fine.
 - **3:07** ~2-3mm should do. This is just to make some room in the printed tool in the next step.
 - **3:44** Ensure not to move Nyloc when fastening the cap nut. 
 - **3:50** Relax the spring, but not entirely. The T-nut should have ~2 full rotations of compression on the spring.
  
{: .note}
>**3:29** The principle function of this tool is to set the position of the Nyloc nut on the right, such that the fixed wwasher is 32.6mm from the same-sized washer on the other side, which also has a locating feature in the tool. The tool acts like a wrench for the Nyloc, so the nut should not rotate when the screw is turned. As the M3 is screwed into the Nyloc, the play (gap) between the Nyloc and the fixed washer is closed, eventually pushing the other washer up against its locating feature. When that happens, we're ready to move on and lock the fixed washer in place from the other side. Below is a more in-depth look at how the tool should be used.
> <iframe src="https://docs.google.com/presentation/d/e/2PACX-1vQnrFP9683292Te3UQBI_oM1244eqARZym0LYXcoMPTrTByoLInpAos08uLyxGXo-lPPDhYonXa4W9M/pubembed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" frameborder="0" width="100%" height="400px" allowfullscreen="true" mozallowfullscreen="true" webkitallowfullscreen="true"></iframe>

 - **3:47** Decompress until the spring is only compressed ~1mm from full extension. The proper force will be calibrated in the Checks and Calibration section.
 - **4:33** Remove support material from Force Sensor Plug.
 - **5:12** Force Sensor Frame Mount should touch the rear vertical extrusion.
 - **5:15** Side B Force Sensor can be assembled now, but wait to install it until the Routing Pod section. Continue to [Y Endstop]({{site.url}}/{{site.baseurl}}/doc_tree/2_assembly/07_auxiliary_modules_2/2_y-endstop.html)

{: .note}
>The compression force of the 'sensors' will be adjusted in the Checks and Calibration section. Part of the complexity in the design of the 'force sensors' was to ensure that they could be:
>- adjusted for compression force without disassembly
>- made from cheap, off-the-shelf components, commonly found in 3D printers
>- repeatable after install, particularly with regard to the wire routing and conducting contacts

---
## Magnet Polarity



---
## Continuity Testing

**Preprequisite:** 
* Set multimeter to continuity mode
* Multimeter continuity mode tested and working (beeps when touching leads)

**Test:**
* Insert the multimeter leads into the Wago connectors as shown.
* With no force applied to the rocker, the multimeter should beep.
* Apply force to the rocker. The beeping should stop, indicating the connection is broken.
* Release the rocker. The multimeter should beep again, confirming the connection has returned.

<span style="color:green">**Pass:** The multimeter beeps with no force, stops beeping when force is applied, and beeps again when the force is released.</span>



---

## Interactive View
<div class="online_3d_viewer"
    model="https://media.githubusercontent.com/media/AutomatedLayers/VertigoMk1/main/docs/assets/3d/force_sensor.glb"
    backgroundcolor="244, 246, 250"
    environmentmap=
    "
    {{site.url}}/{{site.baseurl}}/assets/js/o3dv/envmaps/studio/px.png,
    {{site.url}}/{{site.baseurl}}/assets/js/o3dv/envmaps/studio/nx.png,
    {{site.url}}/{{site.baseurl}}/assets/js/o3dv/envmaps/studio/py.png,
    {{site.url}}/{{site.baseurl}}/assets/js/o3dv/envmaps/studio/ny.png,
    {{site.url}}/{{site.baseurl}}/assets/js/o3dv/envmaps/studio/pz.png,
    {{site.url}}/{{site.baseurl}}/assets/js/o3dv/envmaps/studio/nz.png
    "
    >
</div>

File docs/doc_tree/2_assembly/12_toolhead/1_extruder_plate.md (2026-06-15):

---
title: Extruder Plate
layout: assembly
parent: Toolhead
nav_order: 1
---

# Extruder Plate



{: .important}
Go to the [Configuring the Toolhead Board]({{site.url}}/{{site.baseurl}}/doc_tree/3_wiring/wiring.html#configuring-the-toolhead-board) section of the Wiring Guide to set up the toolhead board before install.

## Materials

| Hardware | Qty | 
|:---|:----|
| E3D Revo PZ Probe Coldside | 1 |
| E3D Revo Heatercore - Vertigo Mk1 edition | 1 |
| E3D Revo Nozzle | 1 |
| Toolhead Plate - CNC Steel | 1 |
| PTFE Tube - 2mm ID | 1 |
| Torsion Spring | 1 |
| Razor Blade: Excel 20005 | 1 |
| LDO Orbiter Extruder | 1 |
| Magnet 1/4in Countersunk | 2 |
| Switch - D2HW | 2 |
| M3x40 SHCS | 2 |
| M3x30 SHCS | 2 |
| M3x14 SHCS | 1 |
| M3x8 SHCS | 1 |
| M3x10 FHCS | 4 |
| M2x16 SHCS | 1 |
| M2x8 SHCS | 4 |
| M2x8 FHCS | 2 |
| M3 Nyloc Nut | 3 |
| M2 Hex Nut | 2 |
| M3x5.7 Brass Insert | 4 |
| Zip Tie | 2 |

| Pogo Pin Cables                      | 
|:-------------------------------------|
| Z-102                                |
| Z-103                                |
| Z-104                                |
| **Heatercore Cables**                | 
| Z-108                                |
| Z-109                                |
| **X Endstop Cable**                  | 
| Z-100                                |
| **PZ Probe Controller Cable**        | 
| Z-107                                |
| **Extruder Motor Cable**             | 
| Z-101                                |

| Printed Parts | Qty |
|:---|:----|
| <a href="https://github.com/AutomatedLayers/VertigoMk1/blob/main/hardware/STL/07%20Hitchcock%20Toolhead/Toolhead/Razor%20Lever%20-%20Bottom.stl" target="_blank">Razor Lever - Bottom</a> | 1 |
| <a href="https://github.com/AutomatedLayers/VertigoMk1/blob/main/hardware/STL/07%20Hitchcock%20Toolhead/Toolhead/Razor%20Lever%20-%20Cap.stl" target="_blank">Razor Lever - Cap</a> | 1 |
| <a href="https://github.com/AutomatedLayers/VertigoMk1/blob/main/hardware/STL/07%20Hitchcock%20Toolhead/Toolhead/Razor%20Lever%20-%20Top.stl" target="_blank">Razor Lever - Top</a> | 1 |
| <a href="https://github.com/AutomatedLayers/VertigoMk1/blob/main/hardware/STL/07%20Hitchcock%20Toolhead/Toolhead/Toolhead%20Board%20Mount.stl" target="_blank">Toolhead Board Mount</a> | 1 |
| <a href="https://github.com/AutomatedLayers/VertigoMk1/blob/main/hardware/STL/07%20Hitchcock%20Toolhead/Toolhead/Toolhead%20Heatbreak%20Riser.stl" target="_blank">Toolhead Heatbreak Riser</a> | 1 |
| <a href="https://github.com/AutomatedLayers/VertigoMk1/blob/main/hardware/STL/07%20Hitchcock%20Toolhead/Toolhead/Toolhead%20Motor%20Arch.stl" target="_blank">Toolhead Motor Arch</a> | 1 |
| <a href="https://github.com/AutomatedLayers/VertigoMk1/blob/main/hardware/STL/07%20Hitchcock%20Toolhead/Toolhead/Toolhead%20Pogo%20Mount.stl" target="_blank">Toolhead Pogo Mount</a> | 1 |

## Animated Assembly

<iframe style='width:100%; height:621px;' src="https://www.youtube.com/embed/ctBYT1iY4fg?si=bYQR5f059U05vn6N" title="YouTube video player" frameborder="0" allow="accelerometer; autoplay; clipboard-write; encrypted-media; gyroscope; picture-in-picture; web-share" referrerpolicy="strict-origin-when-cross-origin" allowfullscreen></iframe>

## Assembly Notes

 - **0:07** Unfortunately the wires that come with the standard E3D HeaterCore were not long enough to reach the toolhead board in our configuration. You must have the modified 'Vertigo Mk1' heater core, or modifiy the wires of your own to reach the board **at your own risk**. We will be releasing STLs of 3D printed tooling along with an instruction video for modifying heater core cables at a later date (WIP).

 - **0:14** A tiny dab of Boron Nitride 'anti-seize' paste on the threads can help prevent the nozzle from unscrewing itself when printing for many continuous hours. This is also why the 'Wall Loop Direction' is set to 'Clockwise' in our [default Slicer settings]({{site.url}}/{{site.baseurl}}/doc_tree/7_slicer/slicer.html). We have also had success with a slightly more aggressive finger-tight approach.
 - **1:48** The arrow is indicating that this hole should be visible.
 - **1:54** The lower M2x8 SHCS acts like a pin to push and pull the razor; it does not screw into anything.
 - **3:36** Magnet polarity graphic is below.
 - **3:51** The flat side of the pogo connector should be on the open-ended side of the Pogo Mount, as shown in the video.
 - **4:15** Make sure the zip tie nub is under the Pogo Mount. It could interfere with the cowl if it is on the side.
 - **5:15** Some LDO Orbiters arrive with the filament guide protruding past the mounting surface. If it protrudes, it may interfere with the cutter. To check, place the Orbiter on a flat surface. If it rocks, the filament guide is protruding. If it sits flat, it is okay. [See graphic below.]({{site.url}}/{{site.baseurl}}/doc_tree/2_assembly/12_toolhead/1_extruder_plate.html#ldo-orbiter).
 - **5:15** If the PTFE tube falls out of the LDO Orbiter, add a small bead of glue or a small piece of tape to increase its diameter. The LDO Orbiter is not designed for this low-profile filament cutting setup, so this short PTFE tube is used as a workaround.
 - **6:04** See the notes in the [PZ Probe Controller]({{site.url}}/{{site.baseurl}}/doc_tree/3_wiring/wiring.html#39-pz-probe-controller-cable-z-105-z-106-z-107) section of the wiring guide for info on the other cables attached to the PZ Probe.
 - **6:15** If you haven't already, go ahead and [configure the toolhead board]({{site.url}}/{{site.baseurl}}/doc_tree/3_wiring/wiring.html#configuring-the-toolhead-board).
 - **7:26** Continue to [Cowl]({{site.url}}/{{site.baseurl}}\doc_tree\2_assembly\12_toolhead\2_cowl.html)

---

#### Magnet Polarity



---

#### LDO Orbiter

* Place the LDO Orbiter mounting surface on a flat surface. 
  * The toolhead board mount sits slightly lower than the Orbiter, so let it hang off the edge of your flat surface.
* Check that the Orbiter does not rock on the filament guide. If it rocks, the filament guide is protruding past the Orbiter mounting surface.
* If the filament guide needs adjustment, check that it does not rub against the extruder gears. You can rotate the gear by gently pushing it with a small flathead screwdriver.





{: .warning }
If the LDO Orbiter is adjusted too far upward, the filament guide may rub against the extruder gears during filament feeding.

---

## Interactive View
<div class="online_3d_viewer"
    model="https://media.githubusercontent.com/media/AutomatedLayers/VertigoMk1/main/docs/assets/3d/toolhead_plate.glb"
    backgroundcolor="244, 246, 250"
    environmentmap=
    "
    {{site.url}}/{{site.baseurl}}/assets/js/o3dv/envmaps/studio/px.png,
    {{site.url}}/{{site.baseurl}}/assets/js/o3dv/envmaps/studio/nx.png,
    {{site.url}}/{{site.baseurl}}/assets/js/o3dv/envmaps/studio/py.png,
    {{site.url}}/{{site.baseurl}}/assets/js/o3dv/envmaps/studio/ny.png,
    {{site.url}}/{{site.baseurl}}/assets/js/o3dv/envmaps/studio/pz.png,
    {{site.url}}/{{site.baseurl}}/assets/js/o3dv/envmaps/studio/nz.png
    "
    >
</div>

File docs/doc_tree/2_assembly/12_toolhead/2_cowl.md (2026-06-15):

---
title: Cowl
layout: assembly
parent: Toolhead
nav_order: 2
---

# Rear Cover & Cowl



## Materials

| Hardware | Qty | 
|:---|:----|
| Cowl PCB | 1 |
| Magnet 1/4in Countersunk | 4 |
| Radial Fan - 3010 | 4 |
| Nozzle LED | 1 |
| Cowl Logo LED | 1 |
| M3x8 SHCS | 2 |
| M2x8 SHCS | 1 |
| M2x16 SHCS | 1 |
| M2x8 FHCS | 4 |
| M3 Nyloc Nut | 3 |
| M2 Hex Nut | 2 |
| M3x5.7 Brass Insert | 2 |

| Part Cooling Fan Cables              | 
|:-------------------------------------|
| Z-117                                |
| Z-118                                |
| Z-119                                |
| **Heatsink Fan Cable**               | 
| Z-120                                |
| **Nozzle LED Cable**                 | 
| Z-98                                 |
| **Logo LED Cable**                   | 
| Z-99                                 |

| Printed Parts | Qty |
|:---|:----|
| <a href="https://github.com/AutomatedLayers/VertigoMk1/blob/main/hardware/STL/07%20Hitchcock%20Toolhead/Cowl/Fan%20Screw%20Spacer%20-%20Q2.stl" target="_blank">Fan Screw Spacer</a> | 2 |
| <a href="https://github.com/AutomatedLayers/VertigoMk1/blob/main/hardware/STL/07%20Hitchcock%20Toolhead/Cowl/Toolhead%20Cowl%20-%20Accent.stl" target="_blank">Toolhead Cowl</a> | 1 |
| <a href="https://github.com/AutomatedLayers/VertigoMk1/blob/main/hardware/STL/07%20Hitchcock%20Toolhead/Cowl/Toolhead%20Cowl%20Heatbreak%20Duct.stl" target="_blank">Toolhead Cowl Heatbreak Duct</a> | 1 |
| <a href="https://github.com/AutomatedLayers/VertigoMk1/blob/main/hardware/STL/07%20Hitchcock%20Toolhead/Cowl/Toolhead%20Cowl%20Logo%20Insert%20-%20Transparent.stl" target="_blank">Toolhead Cowl Logo Insert</a> | 1 |
| <a href="https://github.com/AutomatedLayers/VertigoMk1/blob/main/hardware/STL/07%20Hitchcock%20Toolhead/Cowl/Toolhead%20Cowl%20Logo%20Insert%20Clip%20-%20Transparent.stl" target="_blank">Toolhead Cowl Logo Insert Clip</a> | 1 |
| <a href="https://github.com/AutomatedLayers/VertigoMk1/blob/main/hardware/STL/07%20Hitchcock%20Toolhead/Cowl/Toolhead%20Cowl%20Logo.stl" target="_blank">Toolhead Cowl Logo</a> | 1 |

## Animated Assembly

<iframe style='width:100%; height:621px;' src="https://www.youtube.com/embed/ctBYT1iY4fg?si=xTGWx75-QHBdLExk&amp;start=466" title="YouTube video player" frameborder="0" allow="accelerometer; autoplay; clipboard-write; encrypted-media; gyroscope; picture-in-picture; web-share" referrerpolicy="strict-origin-when-cross-origin" allowfullscreen></iframe>

## Assembly Notes
 - **8:02** Magnet polarity graphic is below.
 - **10:20** This is easiest with the back of the Cowl (the open part) face up so gravity can help. M2 screws can be loosely threaded while while cables are checked and adjusted.
 - **10:42** Optional, but recommended to keep the Logo Insert Clip attached.
 - **11:32** The Cowl is fairly tough, but just be careful not bend it too much.
 - **12:00** Always remove the Cowl and Rear Cover before installing or removing the Extruder Plate assembly.
 - **12:07** One day, maybe E3D will make a Revo HeaterCore where the wires exit vertically; but until that day, please be careful with the strain relief when installing or removing. Tilting the top of the Extruder Plate assembly back slightly so that it makes contact in the rear first when pulled by the magnets can help with this. 

---

#### Magnet Polarity





---

## Interactive View
<div class="online_3d_viewer"
    model="https://media.githubusercontent.com/media/AutomatedLayers/VertigoMk1/main/docs/assets/3d/toolhead_cowl.glb"
    backgroundcolor="244, 246, 250"
    environmentmap=
    "
    {{site.url}}/{{site.baseurl}}/assets/js/o3dv/envmaps/studio/px.png,
    {{site.url}}/{{site.baseurl}}/assets/js/o3dv/envmaps/studio/nx.png,
    {{site.url}}/{{site.baseurl}}/assets/js/o3dv/envmaps/studio/py.png,
    {{site.url}}/{{site.baseurl}}/assets/js/o3dv/envmaps/studio/ny.png,
    {{site.url}}/{{site.baseurl}}/assets/js/o3dv/envmaps/studio/pz.png,
    {{site.url}}/{{site.baseurl}}/assets/js/o3dv/envmaps/studio/nz.png
    "
    >
</div>

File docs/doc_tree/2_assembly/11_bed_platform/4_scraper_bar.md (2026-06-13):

---
title: Scraper Bar
layout: assembly
parent: Bed Platform
nav_order: 4
---

# Scraper Bar



## Materials

| Hardware | Qty | 
|:---|:----|
| Extrusion - 1010-300 | 1 |
| Makerbeam M3 T-Nut | 14  |
| Magnet - 1/4in Cube | 2 |
| Plastic Scraper | 7 |
| Magnet - 6x3mm | 21  |
| M1.5x10 Dowel | 28  |
| Linear Spring | 2 |
| M3x5.7 Brass Insert | 10  |
| M3x25 SHCS | 4 |
| M3x20 SHCS | 2 |
| M3x16 SHCS | 8 |
| M3x10 SHCS | 15  |
| M2x8 FHCS | 4 |

| Printed Parts | Qty |
|:---|:----|
| <a href="https://github.com/AutomatedLayers/VertigoMk1/blob/main/hardware/STL/06%20Bed%20Platform/Scraper%20Bar/Linear%20Spring%20Bushing%20Inner%20-%20Q2.stl" target="_blank">Linear Spring Bushing Inner</a> | 2 |
| <a href="https://github.com/AutomatedLayers/VertigoMk1/blob/main/hardware/STL/06%20Bed%20Platform/Scraper%20Bar/Linear%20Spring%20Bushing%20Outer%20-%20Q2.stl" target="_blank">Linear Spring Bushing Outer</a> | 2 |
| <a href="https://github.com/AutomatedLayers/VertigoMk1/blob/main/hardware/STL/06%20Bed%20Platform/Scraper%20Bar/Scraper%20Bar%20Height%20Adjustment%20Block%20-%20Accent%20-%2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" target="_blank">Scraper Bar Height Adjustment Block</a> | 2 |
| <a href="https://github.com/AutomatedLayers/VertigoMk1/blob/main/hardware/STL/06%20Bed%20Platform/Scraper%20Bar/Scraper%20Bar%20Wing%20A.stl" target="_blank">Scraper Bar Wing A</a> | 1 |
| <a href="https://github.com/AutomatedLayers/VertigoMk1/blob/main/hardware/STL/06%20Bed%20Platform/Scraper%20Bar/Scraper%20Bar%20Wing%20B.stl" target="_blank">Scraper Bar Wing B</a> | 1 |
| <a href="https://github.com/AutomatedLayers/VertigoMk1/blob/main/hardware/STL/06%20Bed%20Platform/Scraper%20Bar/Scraper%20Bar%20Wing%20Dog%20Bone%20-%20Q2.stl" target="_blank">Scraper Bar Wing Dog Bone</a> | 2 |
| <a href="https://github.com/AutomatedLayers/VertigoMk1/blob/main/hardware/STL/06%20Bed%20Platform/Scraper%20Bar/Scraper%20Bar%20Wing%20Frame%20Wedge%20A%20-%20Accent.stl" target="_blank">Scraper Bar Wing Frame Wedge A</a> | 1 |
| <a href="https://github.com/AutomatedLayers/VertigoMk1/blob/main/hardware/STL/06%20Bed%20Platform/Scraper%20Bar/Scraper%20Bar%20Wing%20Frame%20Wedge%20B%20-%20Accent.stl" target="_blank">Scraper Bar Wing Frame Wedge B</a> | 1 |
| <a href="https://github.com/AutomatedLayers/VertigoMk1/blob/main/hardware/STL/06%20Bed%20Platform/Scraper%20Bar/Scraper%20Module%20Bed%20Cam%20-%20Q7.stl" target="_blank">Scraper Module Bed Cam</a> | 7 |
| <a href="https://github.com/AutomatedLayers/VertigoMk1/blob/main/hardware/STL/06%20Bed%20Platform/Scraper%20Bar/Scraper%20Module%20End%20Effector%20-%20Q7.stl" target="_blank">Scraper Module End Effector</a> | 7 |
| <a href="https://github.com/AutomatedLayers/VertigoMk1/blob/main/hardware/STL/06%20Bed%20Platform/Scraper%20Bar/Scraper%20Module%20Frame%20Mount%20-%20Q7.stl" target="_blank">Scraper Module Frame Mount</a> | 7 |

## Animated Assembly

<iframe style='width:100%; height:621px;' src="https://www.youtube.com/embed/beljLD9yPFU?si=ZPCdjsPRfDH1dlFw&amp;start=569" title="YouTube video player" frameborder="0" allow="accelerometer; autoplay; clipboard-write; encrypted-media; gyroscope; picture-in-picture; web-share" referrerpolicy="strict-origin-when-cross-origin" allowfullscreen></iframe>

## Assembly Notes

 - **10:09** This insert is to keep the adjutment screw from coming out when using it to raise or lower the Scraper Bar. It will rotate with the screw.
 - **10:33** It's recommended to use some glue on the threads of these M2x8 FHCS.
 - **10:52** The Linear Spring should extend and retract with minimal friction. **Be careful not to pull too much of the spring out; it will coil up on itself and be difficult to untangle or could damage the spring.**
 - **11:04** Refer to the magnetic polarity information below for details. **Note the orientation of the Wedge when the magnet is installed**.
 - **12:47** Only one end of the scraper bar is screwed in. This allows the distance between the carriages on the bed rails to define the distance between the Scraper Bar Wings. Scraper Modules should fit roughly centered between the two Scraper Bar Wings, with minimal gap between them, able to be independently articulated.
 - **13:24** Scraper Modules should not be tight against the bed. All the blades should just touch the print surface. Check for gaps between the blades and the print surface on either side of the Scraper Bar to make it level.
 - **13:40** Use a 1.5mm or 2mm Hex Key. It will be difficult to get the key into the spring clip if the Scraper Bar is too far forward.
 - **13:57** Ideally the Scraper Bar should return on its own, even when the bed is vertical. The magnets will ensure the Scraper Bar returns when vertical and prevent any unsightly stick slip.
 - **14:23** You may apply a bit of threadlocker on the Kinematic Seatbelt screws now. This is more useful on side A, as side B will be locked in place.
 - **14:30** The M3 in the Dowel Cap on side A does **not** need loosening here. Keep it snug.
 - **14:30** Reminder that only side B has Seatbelt Locks

---
#### Magnet Polarity



---
## Interactive Views

#### Scraper Bar
<div class="online_3d_viewer"
    model="https://media.githubusercontent.com/media/AutomatedLayers/VertigoMk1/main/docs/assets/3d/bed_scraper.glb"
    backgroundcolor="244, 246, 250"
    environmentmap=
    "
    {{site.url}}/{{site.baseurl}}/assets/js/o3dv/envmaps/studio/px.png,
    {{site.url}}/{{site.baseurl}}/assets/js/o3dv/envmaps/studio/nx.png,
    {{site.url}}/{{site.baseurl}}/assets/js/o3dv/envmaps/studio/py.png,
    {{site.url}}/{{site.baseurl}}/assets/js/o3dv/envmaps/studio/ny.png,
    {{site.url}}/{{site.baseurl}}/assets/js/o3dv/envmaps/studio/pz.png,
    {{site.url}}/{{site.baseurl}}/assets/js/o3dv/envmaps/studio/nz.png
    "
    >
</div>

#### Scraper Module
<div class="online_3d_viewer"
    model="https://media.githubusercontent.com/media/AutomatedLayers/VertigoMk1/main/docs/assets/3d/bed_scraper_module.glb"
    backgroundcolor="244, 246, 250"
    environmentmap=
    "
    {{site.url}}/{{site.baseurl}}/assets/js/o3dv/envmaps/studio/px.png,
    {{site.url}}/{{site.baseurl}}/assets/js/o3dv/envmaps/studio/nx.png,
    {{site.url}}/{{site.baseurl}}/assets/js/o3dv/envmaps/studio/py.png,
    {{site.url}}/{{site.baseurl}}/assets/js/o3dv/envmaps/studio/ny.png,
    {{site.url}}/{{site.baseurl}}/assets/js/o3dv/envmaps/studio/pz.png,
    {{site.url}}/{{site.baseurl}}/assets/js/o3dv/envmaps/studio/nz.png
    "
    >
</div>

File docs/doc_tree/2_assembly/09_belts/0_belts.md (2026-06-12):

---
title: Belts
layout: assembly
parent: Assembly Guide
nav_order: 9
---

# Belts

{: .important}
>Before installing the X/Y belts, loosen the A/B steppers and clamp plate (via the access holes in the XY Drive Housing Lids, if installed). Rotate the tensioning handles and push the cam sliders toward the outside of the printer such that the belts will travel the shortest path, giving maximum travel for tensioning.
>
>For the Z Belts, (watch the video) before the belt is fed around the tensioning pulley, adjust the tensioning knob such that the bottom of the tensioner is about 7mm below the inside edge of the pocket in the foot where it sits. This ensures plenty of room for tensioning and a relatively consistent belt length and frequency. An update was made to the [Foot Z Tensioner](https://github.com/AutomatedLayers/VertigoMk1/blob/main/hardware/STL/02%20Feet/All%20Feet/Foot%20Z%20Tensioner%20-%20Accent%20-%20Q4.stl) to place a line that should line up with the lip of the inside edge of the tensioner pocket when the tensioner is at the right starting point.

## Animated Assembly

<iframe style='width:100%; height:621px;' src="https://www.youtube.com/embed/qt9ShgclVMk?si=CSxEvuF-HaGxkTM7" title="YouTube video player" frameborder="0" allow="accelerometer; autoplay; clipboard-write; encrypted-media; gyroscope; picture-in-picture; web-share" referrerpolicy="strict-origin-when-cross-origin" allowfullscreen></iframe>

---

## Belt Tension Guide

{: .note}
If you want an easy way to tension your belts without using an app to measure frequency, check out the [PF Makes Belt Tension Meter](https://github.com/Diyshift/3D-Printer/tree/main/GT2%20Belt%20Tension%20Meter) which can also be [purchased through West3D](https://west3d.com/products/complete-kit-of-3d-printer-belt-tension-meter-by-pf-makes-special-west3d-edition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). The manual on this project's GitHub repo is full of good information.

Proper belt tension ensures accurate motion and prevents skipped steps. Too loose and the belt will slip; too tight and it adds unnecessary load to the motor bearings. Tension is set by plucking the free span of the belt like a guitar string and measuring the resulting vibration frequency with a phone app. You could also use a belt tension force gauge if you're cool enough to have one.

The target frequency for a given tension is derived from the string vibration formula:

$$f = \frac{1}{2L} \sqrt{\frac{F}{\mu}}$$

where `L` is the free span in meters, `F` is the desired tension in Newtons, and `μ` is the linear mass density of the belt in kg/m.

---
### Belt Spans to Tune
XY Belt Span

<div align="center">
  Z Belt Span
</div>
<!-- ![]({{site.url}}/{{site.baseurl}}/assets/images/z_belt_span.webp) -->

---

### Target Frequencies

#### X/Y Axis Belts

| Parameter | Value |
|---|---|
| Belt | Gates PowerGrip 2GT · 2mm Pitch · 6mm Width |
| Free span | 0.390 m |
| Linear density (μ) | 0.0083 kg/m |
| Target tension | 26.69 N (6 lbf) |
| **Target frequency** | **73.2 Hz** |

#### Z Axis Belts

| Parameter | Value |
|---|---|
| Belt | Gates PowerGrip 2GT · 2mm Pitch · 9mm Width |
| Free span | 0.534 m |
| Linear density (μ) | 0.01245 kg/m |
| Target tension | 40.03 N (9 lbf) |
| **Target frequency** | **83.8 Hz** |

---

### Measurement Procedure

1. Confirm the **free span** — the unsupported belt length between contact points with nothing touching it
2. Pluck the belt near the **middle** of the span, like a guitar string
3. Measure the frequency with a phone app:
   - **Android:** Spectroid — use FFT mode at the highest FFT size
   - **iOS:** Physics Toolbox Sensor Suite
4. Adjust tension until the fundamental frequency matches your axis target above
5. Re-measure after each adjustment — tension can shift slightly as the belt settles
6. You may have to go back an forth a bit, as the tension in one belt can impact the other. If it's difficult to get them both to measure equal frequency and correct frequency, its better to have them be equal. Unequal tension can cause the gantry to skew.

---

{: .note}
>- Gates recommends **6–8 lbf** for 6mm GT belts in a registration drive; the 9mm Z target of 9 lbf scales proportionally with width
>- Ensure **nothing contacts the belt** along the free span during measurement
>- If the reading is noisy, pluck more firmly or reduce nearby vibrations
>- These figures assume **genuine Gates 2GT belt** — third-party belts vary in density and will give inaccurate results with this formula

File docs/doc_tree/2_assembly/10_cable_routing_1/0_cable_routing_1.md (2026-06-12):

---
title: Rear Panel & E-Chains
layout: assembly
parent: Assembly Guide
nav_order: 10
---

# Rear Panel & E-Chains

## Materials

| Hardware - Rear Panel | Qty | 
|:---|:----|
| Weather Stripping  6mm x 1.6mm | |
| Rear Panel | 1 |
| M3x5.7 Brass Insert | 10  |
| M3x12 SHCS | 2 |
| M5x10 BHCS | 14  |
| M5 Roll-In Nut | 14  |
| M3 Roll-In Nut | 2 |
| **Hardware - E-Chains** | | 
| Drag Chain, R-15, 31 links | 1 |
| Drag Chain, R-15, 31 links | 1 |
| Brass Bushing - Flange | 1 |
| M3x5.7 Brass Insert | 2 |
| M3x12 SHCS | 1 |
| M3x8 FHCS | 2 |

| Bed Cables                           | 
|:-------------------------------------|
| Z-46 - Z-52                          |

| Toolhead Cables                      | 
|:-------------------------------------|
| Z-53 - Z-56                          |

| Printed Parts | Qty |
|:---|:----|
| <a href="https://github.com/AutomatedLayers/VertigoMk1/blob/main/hardware/STL/08%20Enclosure/Rear%20Panel%20Mount%20-%20Bottom%20Corner%20A.stl" target="_blank">Rear Panel Mount - Bottom Corner A</a> | 1 |
| <a href="https://github.com/AutomatedLayers/VertigoMk1/blob/main/hardware/STL/08%20Enclosure/Rear%20Panel%20Mount%20-%20Bottom%20Corner%20B.stl" target="_blank">Rear Panel Mount - Bottom Corner B</a> | 1 |
| <a href="https://github.com/AutomatedLayers/VertigoMk1/blob/main/hardware/STL/08%20Enclosure/Rear%20Panel%20Mount%20-%20Center%20A.stl" target="_blank">Rear Panel Mount - Center A</a> | 1 |
| <a href="https://github.com/AutomatedLayers/VertigoMk1/blob/main/hardware/STL/08%20Enclosure/Rear%20Panel%20Mount%20-%20Center%20B.stl" target="_blank">Rear Panel Mount - Center B</a> | 1 |
| <a href="https://github.com/AutomatedLayers/VertigoMk1/blob/main/hardware/STL/08%20Enclosure/Rear%20Panel%20Mount%20-%20Top%20Corner%20A.stl" target="_blank">Rear Panel Mount - Top Corner A</a> | 1 |
| <a href="https://github.com/AutomatedLayers/VertigoMk1/blob/main/hardware/STL/08%20Enclosure/Rear%20Panel%20Mount%20-%20Top%20Corner%20B.stl" target="_blank">Rear Panel Mount - Top Corner B</a> | 1 |
| <a href="https://github.com/AutomatedLayers/VertigoMk1/blob/main/hardware/STL/10%20Auxilliary%20Modules%20%26%20Cable%20Routing/Cable%20Chain/Frame%20Cable%20Chain%20Mount.st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" target="_blank">Frame Cable Chain Mount</a> | 1 |
| <a href="https://github.com/AutomatedLayers/VertigoMk1/blob/main/hardware/STL/07%20Hitchcock%20Toolhead/Toolhead/E-Chain%20Interface%20Bushing%20M.stl" target="_blank">E-Chain Interface Bushing M</a> | 1 |
| <a href="https://github.com/AutomatedLayers/VertigoMk1/blob/main/hardware/STL/07%20Hitchcock%20Toolhead/Toolhead/E-Chain%20Interface%20Bushing%20F.stl" target="_blank">E-Chain Interface Bushing F</a> | 1 |
| <a href="https://github.com/AutomatedLayers/VertigoMk1/blob/main/hardware/STL/07%20Hitchcock%20Toolhead/Toolhead/E-Chain%20Interface.stl" target="_blank">E-Chain Interface</a> | 1 |
| <a href="https://github.com/AutomatedLayers/VertigoMk1/blob/main/hardware/STL/00%20Tools/Bed%20Chain%20Cable%20Setter%20Tool.STL" target="_blank">Bed Chain Cable Setter Tool</a> | 1 |

## Animated Assembly

<iframe style='width:100%; height:621px;' src="https://www.youtube.com/embed/6_mASbAlG5Y?si=N3sbqahR8ou72ulu" title="YouTube video player" frameborder="0" allow="accelerometer; autoplay; clipboard-write; encrypted-media; gyroscope; picture-in-picture; web-share" referrerpolicy="strict-origin-when-cross-origin" allowfullscreen></iframe>

## Assembly Notes

**E-Chain Assembly Example**

<iframe style='width:100%; height:621px;' src="https://www.youtube.com/embed/x76eqS1hyPU?si=e7mVZvqrAoURul04" title="YouTube video player" frameborder="0" allow="accelerometer; autoplay; clipboard-write; encrypted-media; gyroscope; picture-in-picture; web-share" referrerpolicy="strict-origin-when-cross-origin" allowfullscreen></iframe>

<!-- ## Interactive View

<div class="online_3d_viewer"
    model="https://media.githubusercontent.com/media/AutomatedLayers/VertigoMk1/main/docs/assets/3d/chain_mount.glb"
    backgroundcolor="244, 246, 250"
    environmentmap=
    "
    {{site.url}}/{{site.baseurl}}/assets/js/o3dv/envmaps/studio/px.png,
    {{site.url}}/{{site.baseurl}}/assets/js/o3dv/envmaps/studio/nx.png,
    {{site.url}}/{{site.baseurl}}/assets/js/o3dv/envmaps/studio/py.png,
    {{site.url}}/{{site.baseurl}}/assets/js/o3dv/envmaps/studio/ny.png,
    {{site.url}}/{{site.baseurl}}/assets/js/o3dv/envmaps/studio/pz.png,
    {{site.url}}/{{site.baseurl}}/assets/js/o3dv/envmaps/studio/nz.png
    "
    >
</div> -->

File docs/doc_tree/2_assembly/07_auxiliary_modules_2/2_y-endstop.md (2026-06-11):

---
title: Y Endstop
layout: assembly
parent: Auxiliary Modules Pt. 2
nav_order: 2
---

# Y Endstop


## Materials

| Hardware | Qty | 
|:---|:----|
| M3x5.7 Brass Insert | 2 |
| M3x8 SHCS | 2 |
| M3x16 SHCS | 2 |
| M3 Roll-In Nut | 2 |

| Cables                               | 
|:-------------------------------------|
| Z-72                                 |

| Printed Parts | Qty |
|:---|:----|
| <a href="https://github.com/AutomatedLayers/VertigoMk1/blob/main/hardware/STL/10%20Auxilliary%20Modules%20%26%20Cable%20Routing/Endstops%20%26%20Cable%20Routing/Y%20Endstop%2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" target="_blank">Y Endstop Pod</a> | 1 |
| <a href="https://github.com/AutomatedLayers/VertigoMk1/blob/main/hardware/STL/10%20Auxilliary%20Modules%20%26%20Cable%20Routing/Endstops%20%26%20Cable%20Routing/Y%20Endstop%2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" target="_blank">Y Endstop Pod Cap</a> | 1 |
| <a href="https://github.com/AutomatedLayers/VertigoMk1/blob/main/hardware/STL/10%20Auxilliary%20Modules%20%26%20Cable%20Routing/Endstops%20%26%20Cable%20Routing/Cable%20Cover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" target="_blank">Cable Cover 55mm</a> | 1  |

## Animated Assembly
<iframe style='width:100%; height:621px;' src="https://www.youtube.com/embed/C0KE_nT1YOo?si=bt00TVDFhj8J_SiP&amp;start=327"  title="YouTube video player" frameborder="0" allow="accelerometer; autoplay; clipboard-write; encrypted-media; gyroscope; picture-in-picture; web-share" referrerpolicy="strict-origin-when-cross-origin" allowfullscreen></iframe>

## Assembly Notes

 - **5:43** Make sure the Force Sensor wires are routing into the channel in the Y Endstop Pod.
 - **6:42** Continue to [Safety Switch]({{site.url}}/{{site.baseurl}}/doc_tree/2_assembly/07_auxiliary_modules_2/3_safety_switch.html)

## Interactive View
<div class="online_3d_viewer"
    model="https://media.githubusercontent.com/media/AutomatedLayers/VertigoMk1/main/docs/assets/3d/y_endstop.glb"
    backgroundcolor="244, 246, 250"
    environmentmap=
    "
    {{site.url}}/{{site.baseurl}}/assets/js/o3dv/envmaps/studio/px.png,
    {{site.url}}/{{site.baseurl}}/assets/js/o3dv/envmaps/studio/nx.png,
    {{site.url}}/{{site.baseurl}}/assets/js/o3dv/envmaps/studio/py.png,
    {{site.url}}/{{site.baseurl}}/assets/js/o3dv/envmaps/studio/ny.png,
    {{site.url}}/{{site.baseurl}}/assets/js/o3dv/envmaps/studio/pz.png,
    {{site.url}}/{{site.baseurl}}/assets/js/o3dv/envmaps/studio/nz.png
    "
    >
</div>

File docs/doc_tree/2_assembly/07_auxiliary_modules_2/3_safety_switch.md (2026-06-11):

---
title: Safety Switch
layout: assembly
parent: Auxiliary Modules Pt. 2
nav_order: 3
---

# Safety Switch


## Materials

| Hardware | Qty | 
|:---|:----|
| D2HW-C202MR Switch | 1 |
| M3x10 SHCS | 1 |
| M3x8 SHCS | 1 |
| M3 Roll-In Nut | 1 |

| Cables                                | 
|:--------------------------------------|
| Z-114                                 |
| Z-115                                 |

| Printed Parts | Qty |
|:---|:----|
| <a href="https://github.com/AutomatedLayers/VertigoMk1/blob/main/hardware/STL/10%20Auxilliary%20Modules%20%26%20Cable%20Routing/Safety%20Switch/Safety%20Switch%20Bracket.stl" target="_blank">Safety Switch Bracket</a> | 1 |
| <a href="https://github.com/AutomatedLayers/VertigoMk1/blob/main/hardware/STL/10%20Auxilliary%20Modules%20%26%20Cable%20Routing/Endstops%20%26%20Cable%20Routing/Cable%20Cover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" target="_blank">Cable Cover 55mm</a> | 1  |

## Animated Assembly
<iframe style='width:100%; height:621px;' src="https://www.youtube.com/embed/C0KE_nT1YOo?si=bt00TVDFhj8J_SiP&amp;start=407" title="YouTube video player" frameborder="0" allow="accelerometer; autoplay; clipboard-write; encrypted-media; gyroscope; picture-in-picture; web-share" referrerpolicy="strict-origin-when-cross-origin" allowfullscreen></iframe>

## Assembly Notes

 - **7:22** This is preliminary. The exact height of the safety switch adjustment screw will be set in the Checks and Calibration section.
 - **7:42** Cables and Hardware are listed in [Force Sensors]({{site.url}}/{{site.baseurl}}/doc_tree/2_assembly/07_auxiliary_modules_2/1_force_sensors.html).
 - **8:08** Continue to [Routing Pod]({{site.url}}/{{site.baseurl}}/doc_tree/2_assembly/07_auxiliary_modules_2/4_routing_pod.html)

## Interactive View
<div class="online_3d_viewer"
    model="https://media.githubusercontent.com/media/AutomatedLayers/VertigoMk1/main/docs/assets/3d/safety_switch.glb"
    backgroundcolor="244, 246, 250"
    environmentmap=
    "
    {{site.url}}/{{site.baseurl}}/assets/js/o3dv/envmaps/studio/px.png,
    {{site.url}}/{{site.baseurl}}/assets/js/o3dv/envmaps/studio/nx.png,
    {{site.url}}/{{site.baseurl}}/assets/js/o3dv/envmaps/studio/py.png,
    {{site.url}}/{{site.baseurl}}/assets/js/o3dv/envmaps/studio/ny.png,
    {{site.url}}/{{site.baseurl}}/assets/js/o3dv/envmaps/studio/pz.png,
    {{site.url}}/{{site.baseurl}}/assets/js/o3dv/envmaps/studio/nz.png
    "
    camera=
    "
    5.28, 0.43, 0.19,
    5.2, 0.5, 0.1,
    0, 1, 0
    "
    >
</div>

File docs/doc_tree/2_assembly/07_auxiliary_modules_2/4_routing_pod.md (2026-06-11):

---
title: Routing Pod
layout: assembly
parent: Auxiliary Modules Pt. 2
nav_order: 4
---

# Routing Pod


## Materials

| Hardware | Qty | 
|:---|:----|
| M3x5.7 Brass Insert | 2 |
| M3x8 SHCS | 2 |
| M3x16 SHCS | 2 |
| M3 Roll-In Nut | 2 |

| Printed Parts | Qty |
|:---|:----|
| <a href="https://github.com/AutomatedLayers/VertigoMk1/blob/main/hardware/STL/10%20Auxilliary%20Modules%20%26%20Cable%20Routing/Endstops%20%26%20Cable%20Routing/Cable%20Routi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" target="_blank">Cable Routing Pod Cap</a> | 1 |
| <a href="https://github.com/AutomatedLayers/VertigoMk1/blob/main/hardware/STL/10%20Auxilliary%20Modules%20%26%20Cable%20Routing/Endstops%20%26%20Cable%20Routing/Cable%20Routi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" target="_blank">Cable Routing Pod</a> | 1 |
| <a href="https://github.com/AutomatedLayers/VertigoMk1/blob/main/hardware/STL/10%20Auxilliary%20Modules%20%26%20Cable%20Routing/Endstops%20%26%20Cable%20Routing/Cable%20Cover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" target="_blank">Cable Cover 55mm</a> | 1  |

## Animated Assembly
<iframe style='width:100%; height:621px;' src="https://www.youtube.com/embed/C0KE_nT1YOo?si=bt00TVDFhj8J_SiP&amp;start=504"  title="YouTube video player" frameborder="0" allow="accelerometer; autoplay; clipboard-write; encrypted-media; gyroscope; picture-in-picture; web-share" referrerpolicy="strict-origin-when-cross-origin" allowfullscreen></iframe>

## Assembly Notes

 - **8:39** Make sure the Force Sensor wires are routing into the channel in the Routing Pod.
 - **9:19** Continue to [Enclosure Lights]({{site.url}}/{{site.baseurl}}/doc_tree/2_assembly/07_auxiliary_modules_2/5_enclosure_lights.html)

## Interactive View
<div class="online_3d_viewer"
    model="https://media.githubusercontent.com/media/AutomatedLayers/VertigoMk1/main/docs/assets/3d/routing_pod.glb"
    backgroundcolor="244, 246, 250"
    environmentmap=
    "
    {{site.url}}/{{site.baseurl}}/assets/js/o3dv/envmaps/studio/px.png,
    {{site.url}}/{{site.baseurl}}/assets/js/o3dv/envmaps/studio/nx.png,
    {{site.url}}/{{site.baseurl}}/assets/js/o3dv/envmaps/studio/py.png,
    {{site.url}}/{{site.baseurl}}/assets/js/o3dv/envmaps/studio/ny.png,
    {{site.url}}/{{site.baseurl}}/assets/js/o3dv/envmaps/studio/pz.png,
    {{site.url}}/{{site.baseurl}}/assets/js/o3dv/envmaps/studio/nz.png
    "
    >
</div>

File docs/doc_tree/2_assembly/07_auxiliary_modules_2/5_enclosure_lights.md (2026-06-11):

---
title: Enclosure Lights
layout: assembly
parent: Auxiliary Modules Pt. 2
nav_order: 5
---

# Enclosure Lights


## Materials

| Hardware (for each light) | Qty | 
|:---|:----|
| M3x8 SHCS | 2 |
| M5x10 BHCS | 2 |
| M3x4.3 Brass Insert (4.5) | 2 | 
| M5 Roll-In Nut | 2 | 

| Cables                                | 
|:--------------------------------------|
| Z-57                                  |
| Z-58                                  |

| Printed Parts | Qty |
|:---|:----|
| <a href="https://github.com/AutomatedLayers/VertigoMk1/blob/main/hardware/STL/10%20Auxilliary%20Modules%20%26%20Cable%20Routing/Light%20Bars/Frame%20Light%20Bracket%20A%20-%2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" target="_blank">Frame Light Bracket A</a> | 1 |
| <a href="https://github.com/AutomatedLayers/VertigoMk1/blob/main/hardware/STL/10%20Auxilliary%20Modules%20%26%20Cable%20Routing/Light%20Bars/Frame%20Light%20Bracket%20B%20-%2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" target="_blank">Frame Light Bracket B</a> | 1 |

## Animated Assembly
<iframe style='width:100%; height:621px;' src="https://www.youtube.com/embed/C0KE_nT1YOo?si=bt00TVDFhj8J_SiP&amp;start=562" title="YouTube video player" frameborder="0" allow="accelerometer; autoplay; clipboard-write; encrypted-media; gyroscope; picture-in-picture; web-share" referrerpolicy="strict-origin-when-cross-origin" allowfullscreen></iframe>

## Assembly Notes

{: .important} 
Watch to the end and see the wiring image below before installing.

---

#### Enclosure Light Wiring


---

## Interactive View
<div class="online_3d_viewer"
    model="https://media.githubusercontent.com/media/AutomatedLayers/VertigoMk1/main/docs/assets/3d/enclosure_light.glb"
    backgroundcolor="244, 246, 250"
    camera="
        0.015656794094657564, 0.6521615895459374, -0.0015,
        -0.1846731059284783, 0.6492972234177983, 0.001896061592600428,
        0, 1, 0
    "
    environmentmap=
    "
    {{site.url}}/{{site.baseurl}}/assets/js/o3dv/envmaps/studio/px.png,
    {{site.url}}/{{site.baseurl}}/assets/js/o3dv/envmaps/studio/nx.png,
    {{site.url}}/{{site.baseurl}}/assets/js/o3dv/envmaps/studio/py.png,
    {{site.url}}/{{site.baseurl}}/assets/js/o3dv/envmaps/studio/ny.png,
    {{site.url}}/{{site.baseurl}}/assets/js/o3dv/envmaps/studio/pz.png,
    {{site.url}}/{{site.baseurl}}/assets/js/o3dv/envmaps/studio/nz.png
    "
    >
</div>

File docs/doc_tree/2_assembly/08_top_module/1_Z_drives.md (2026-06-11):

---
title: Z Drives
layout: assembly
parent: Top Module
nav_order: 1
---

# Z Drives


## Materials

| Hardware (for 1 of 4 Z-Drives) | Qty | 
|:---|:----|
| Stepper w/ Gearbox - LDO-17Hs15-1584S-MG5 | 1 |
| GT2 20T Timing Pulley - 9mm Belt | 1 |
| Shaft Coupler | 1 |
| M5x60 D-Shaft | 1 |
| Bearing - 625 | 2 |
| M3x5.7 Brass Insert | 5 |
| M5x10x1 Washer | 4 |
| M5x16 BHCS | 5 |
| M3x40 SHCS | 4 |
| M3x10 SHCS | 3 |
| M5 Roll-In Nut | 5 |

| Printed Parts | Qty |
|:---|:----|
| <a href="https://github.com/AutomatedLayers/VertigoMk1/blob/main/hardware/STL/05%20Top%20Module/Z%20Drives/Z%20Drive%20Housing%20A%20-%20Q2.stl" target="_blank">Z Drive Housing A</a> | 2 |
| <a href="https://github.com/AutomatedLayers/VertigoMk1/blob/main/hardware/STL/05%20Top%20Module/Z%20Drives/Z%20Drive%20Housing%20B%20-%20Q2.stl" target="_blank">Z Drive Housing B</a> | 2 |
| <a href="https://github.com/AutomatedLayers/VertigoMk1/blob/main/hardware/STL/05%20Top%20Module/Z%20Drives/Z%20Drive%20Housing%20Cap%20A%20-%20Q2.stl" target="_blank">Z Drive Housing Cap A</a> | 2 |
| <a href="https://github.com/AutomatedLayers/VertigoMk1/blob/main/hardware/STL/05%20Top%20Module/Z%20Drives/Z%20Drive%20Housing%20Cap%20B%20-%20Q2.stl" target="_blank">Z Drive Housing Cap B</a> | 2 |
| <a href="https://github.com/AutomatedLayers/VertigoMk1/blob/main/hardware/STL/05%20Top%20Module/Z%20Drives/Z%20Motor%20Mount%20A%20-%20Q2.stl" target="_blank">Z Motor Mount A</a> | 2 |
| <a href="https://github.com/AutomatedLayers/VertigoMk1/blob/main/hardware/STL/05%20Top%20Module/Z%20Drives/Z%20Motor%20Mount%20B%20-%20Q2.stl" target="_blank">Z Motor Mount B</a> | 2 |
| <a href="https://github.com/AutomatedLayers/VertigoMk1/blob/main/hardware/STL/00%20Tools/Z%20Drive%20Roll-In%20Nut%20Alignment%20Tool.STL" target="_blank">Z Drive Roll-In Nut Alignment Tool</a> | 1 |

## Animated Assembly

<iframe style='width:100%; height:621px;' src="https://www.youtube.com/embed/treQRNA6tV8?si=PMviitt7CAkCzJvP" title="YouTube video player" frameborder="0" allow="accelerometer; autoplay; clipboard-write; encrypted-media; gyroscope; picture-in-picture; web-share" referrerpolicy="strict-origin-when-cross-origin" allowfullscreen></iframe>

## Assembly Notes

 - **0:41** Should say "Shaft Coupler" instead of "Shaft Collar". Tighten one set screw against the flat face of the D-shaft first, then tighten the other set screw.

## Interactive View
<div class="online_3d_viewer"
    model="https://media.githubusercontent.com/media/AutomatedLayers/VertigoMk1/main/docs/assets/3d/z_drive.glb"
    backgroundcolor="244, 246, 250"
    environmentmap=
    "
    {{site.url}}/{{site.baseurl}}/assets/js/o3dv/envmaps/studio/px.png,
    {{site.url}}/{{site.baseurl}}/assets/js/o3dv/envmaps/studio/nx.png,
    {{site.url}}/{{site.baseurl}}/assets/js/o3dv/envmaps/studio/py.png,
    {{site.url}}/{{site.baseurl}}/assets/js/o3dv/envmaps/studio/ny.png,
    {{site.url}}/{{site.baseurl}}/assets/js/o3dv/envmaps/studio/pz.png,
    {{site.url}}/{{site.baseurl}}/assets/js/o3dv/envmaps/studio/nz.png
    "
    >
</div>

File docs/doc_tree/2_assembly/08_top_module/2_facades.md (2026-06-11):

---
title: Facades
layout: assembly
parent: Top Module
nav_order: 2
---

# Facades, Panel Mount, and Cable Routing


## Materials

| Hardware | Qty | 
|:---|:----|
| M5x10 BHCS | 3 |
| M5 Roll-In Nut | 3 |
| M3x45 SHCS | 6 |
| M3x10 SHCS | 7 |
| M3 Roll-In Nut | 6 |
| M3x5.7 Brass Insert | 7 |

| Printed Parts | Qty |
|:---|:----|
| <a href="https://github.com/AutomatedLayers/VertigoMk1/blob/main/hardware/STL/05%20Top%20Module/Facades/Facade%20Frame%20Front%20-%20Accent.stl" target="_blank">Facade Frame Front</a> | 1 |
| <a href="https://github.com/AutomatedLayers/VertigoMk1/blob/main/hardware/STL/05%20Top%20Module/Facades/Facade%20Frame%20Front%20Insert%20-%20Transparent.stl" target="_blank">Facade Frame Front Insert</a> | 1 |
| <a href="https://github.com/AutomatedLayers/VertigoMk1/blob/main/hardware/STL/05%20Top%20Module/Facades/Facade%20Side%20A.stl" target="_blank">Facade Side A</a> | 1 |
| <a href="https://github.com/AutomatedLayers/VertigoMk1/blob/main/hardware/STL/05%20Top%20Module/Facades/Facade%20Side%20B.stl" target="_blank">Facade Side B</a> | 1 |
| <a href="https://github.com/AutomatedLayers/VertigoMk1/blob/main/hardware/STL/05%20Top%20Module/Facades/Fan%20Grill%20-%20Optional%20-%20Q2.STL" target="_blank">Top Fan Grill</a> | 2 |
| <a href="https://github.com/AutomatedLayers/VertigoMk1/blob/main/hardware/STL/05%20Top%20Module/Facades/Motor%20Facade%20Front%20A.stl" target="_blank">Motor Facade Front A</a> | 1 |
| <a href="https://github.com/AutomatedLayers/VertigoMk1/blob/main/hardware/STL/05%20Top%20Module/Facades/Motor%20Facade%20Front%20B.stl" target="_blank">Motor Facade Front B</a> | 1 |
| <a href="https://github.com/AutomatedLayers/VertigoMk1/blob/main/hardware/STL/05%20Top%20Module/Facades/Motor%20Facade%20Rear%20A.stl" target="_blank">Motor Facade Rear A</a> | 1 |
| <a href="https://github.com/AutomatedLayers/VertigoMk1/blob/main/hardware/STL/05%20Top%20Module/Facades/Motor%20Facade%20Rear%20B.stl" target="_blank">Motor Facade Rear B</a> | 1 |
| <a href="https://github.com/AutomatedLayers/VertigoMk1/blob/main/hardware/STL/05%20Top%20Module/Facades/Top%20Panel%20Latch%20A%20-%20Q2.stl" target="_blank">Top Panel Latch A</a> | 2 |
| <a href="https://github.com/AutomatedLayers/VertigoMk1/blob/main/hardware/STL/05%20Top%20Module/Facades/Top%20Panel%20Latch%20B%20-%20Q2.stl" target="_blank">Top Panel Latch B</a> | 2 |
| <a href="https://github.com/AutomatedLayers/VertigoMk1/blob/main/hardware/STL/05%20Top%20Module/Top%20Panel%20Plate/Top%20Panel%20Plate%20Backstop.stl" target="_blank">Top Panel Plate Backstop</a> | 1 |
| <a href="https://github.com/AutomatedLayers/VertigoMk1/blob/main/hardware/STL/05%20Top%20Module/Top%20Panel%20Plate/Top%20Panel%20Plate%20Cable%20Guide.stl" target="_blank">Top Panel Plate Cable Guide</a> | 1 |
| <a href="https://github.com/AutomatedLayers/VertigoMk1/blob/main/hardware/STL/05%20Top%20Module/Top%20Panel%20Plate/Top%20Panel%20Plate.stl" target="_blank">Top Panel Plate</a> | 1 |

## Animated Assembly

<iframe style='width:100%; height:621px;' src="https://www.youtube.com/embed/mJoSH26DFGI?si=vuDhQvhtAkPRdWh1"  title="YouTube video player" frameborder="0" allow="accelerometer; autoplay; clipboard-write; encrypted-media; gyroscope; picture-in-picture; web-share" referrerpolicy="strict-origin-when-cross-origin" allowfullscreen></iframe>

## Assembly Notes

{: .note}
We don't yet have fans here, but there are places for them in the Facade Sides to allow for future design possibilities, potentially to help exhaust warm air from the top of the chamber to help speed up cooling time between ejections.

## Interactive Views

#### Front Facade
<div class="online_3d_viewer"
    model="https://media.githubusercontent.com/media/AutomatedLayers/VertigoMk1/main/docs/assets/3d/facade_front.glb"
    backgroundcolor="244, 246, 250"
    environmentmap=
    "
    {{site.url}}/{{site.baseurl}}/assets/js/o3dv/envmaps/studio/px.png,
    {{site.url}}/{{site.baseurl}}/assets/js/o3dv/envmaps/studio/nx.png,
    {{site.url}}/{{site.baseurl}}/assets/js/o3dv/envmaps/studio/py.png,
    {{site.url}}/{{site.baseurl}}/assets/js/o3dv/envmaps/studio/ny.png,
    {{site.url}}/{{site.baseurl}}/assets/js/o3dv/envmaps/studio/pz.png,
    {{site.url}}/{{site.baseurl}}/assets/js/o3dv/envmaps/studio/nz.png
    "
    >
</div>

#### Side Facade
<div class="online_3d_viewer"
    model="https://media.githubusercontent.com/media/AutomatedLayers/VertigoMk1/main/docs/assets/3d/facade_side.glb"
    backgroundcolor="244, 246, 250"
    camera="
    -0.5, 0.708, -0.0255,
    -0.174, 0.69, -0.040,
    0, 1, 0
    "
    environmentmap=
    "
    {{site.url}}/{{site.baseurl}}/assets/js/o3dv/envmaps/studio/px.png,
    {{site.url}}/{{site.baseurl}}/assets/js/o3dv/envmaps/studio/nx.png,
    {{site.url}}/{{site.baseurl}}/assets/js/o3dv/envmaps/studio/py.png,
    {{site.url}}/{{site.baseurl}}/assets/js/o3dv/envmaps/studio/ny.png,
    {{site.url}}/{{site.baseurl}}/assets/js/o3dv/envmaps/studio/pz.png,
    {{site.url}}/{{site.baseurl}}/assets/js/o3dv/envmaps/studio/nz.png
    "
    >
</div>

#### Rear Plate and Cable Guide
<div class="online_3d_viewer"
    model="https://media.githubusercontent.com/media/AutomatedLayers/VertigoMk1/main/docs/assets/3d/rear_plate.glb"
    backgroundcolor="244, 246, 250"
    environmentmap=
    "
    {{site.url}}/{{site.baseurl}}/assets/js/o3dv/envmaps/studio/px.png,
    {{site.url}}/{{site.baseurl}}/assets/js/o3dv/envmaps/studio/nx.png,
    {{site.url}}/{{site.baseurl}}/assets/js/o3dv/envmaps/studio/py.png,
    {{site.url}}/{{site.baseurl}}/assets/js/o3dv/envmaps/studio/ny.png,
    {{site.url}}/{{site.baseurl}}/assets/js/o3dv/envmaps/studio/pz.png,
    {{site.url}}/{{site.baseurl}}/assets/js/o3dv/envmaps/studio/nz.png
    "
    >
</div>

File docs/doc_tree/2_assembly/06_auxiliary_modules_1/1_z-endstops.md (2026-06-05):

---
title: Z Endstops
layout: assembly
parent: Auxiliary Modules Pt. 1
nav_order: 2
---

# Z Endstops


{: .important}
This is the first section where cables are installed, so it's a good time to check out the section of the Wiring Guide: [Understanding the Wiring Diagram & Cable Spec]({{site.url}}/{{site.baseurl}}/doc_tree/3_wiring/wiring.html#understanding-the-wiring-diagram--cable-spec)

## Materials

| Hardware (for 1 of 4 pods) | Qty | 
|:---|:----|
| Z Endstop Switch PCB | 1 |
| M3 Roll-In Nut | 2 |
| M3x20 FHCS | 2 |

| Cables                               | 
|:-------------------------------------|
| Z-68                                 |
| Z-69                                 |
| Z-70                                 |
| Z-71                                 |

| Printed Parts | Qty |
|:---|:----|
| <a href="https://github.com/AutomatedLayers/VertigoMk1/blob/main/hardware/STL/10%20Auxilliary%20Modules%20%26%20Cable%20Routing/Endstops%20%26%20Cable%20Routing/Cable%20Cover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" target="_blank">Cable Cover 10mm</a> | 2  |
| <a href="https://github.com/AutomatedLayers/VertigoMk1/blob/main/hardware/STL/10%20Auxilliary%20Modules%20%26%20Cable%20Routing/Endstops%20%26%20Cable%20Routing/Cable%20Cover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" target="_blank">Cable Cover 25mm</a> | 4  |
| <a href="https://github.com/AutomatedLayers/VertigoMk1/blob/main/hardware/STL/10%20Auxilliary%20Modules%20%26%20Cable%20Routing/Endstops%20%26%20Cable%20Routing/Cable%20Cover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" target="_blank">Cable Cover 55mm</a> | 2  |
| <a href="https://github.com/AutomatedLayers/VertigoMk1/blob/main/hardware/STL/10%20Auxilliary%20Modules%20%26%20Cable%20Routing/Endstops%20%26%20Cable%20Routing/Cable%20Cover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" target="_blank">Cable Cover 240mm</a> | 2  |
| <a href="https://github.com/AutomatedLayers/VertigoMk1/blob/main/hardware/STL/10%20Auxilliary%20Modules%20%26%20Cable%20Routing/Endstops%20%26%20Cable%20Routing/Cable%20Gutte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" target="_blank">Cable Gutter - Z Endstop Center</a> | 1  |
| <a href="https://github.com/AutomatedLayers/VertigoMk1/blob/main/hardware/STL/10%20Auxilliary%20Modules%20%26%20Cable%20Routing/Endstops%20%26%20Cable%20Routing/Z%20Endstop%2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" target="_blank">Z Endstop Pod</a> | 4  |
| <a href="https://github.com/AutomatedLayers/VertigoMk1/blob/main/hardware/STL/10%20Auxilliary%20Modules%20%26%20Cable%20Routing/Endstops%20%26%20Cable%20Routing/Z%20Endstop%2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" target="_blank">Z Endstop Pod Cap</a> | 4  |

## Animated Assembly
<iframe style='width:100%; height:621px;' src="https://www.youtube.com/embed/QfOSu2yNCmc?si=UZh_bVq0Q3KChDJH" title="YouTube video player" frameborder="0" allow="accelerometer; autoplay; clipboard-write; encrypted-media; gyroscope; picture-in-picture; web-share" referrerpolicy="strict-origin-when-cross-origin" allowfullscreen></iframe>

## Assembly Notes

{: .important}
>**0:15** These are **NOT** the cables that come in the packages with the endstop PCBs. The correct cables will be labeled and packaged with the rest of the cable bundles.

 - **0:24** Sandwich the Z Endstop Switch PCB between the Z Enstop Pod and Z Endstop Pod Cap, ensuring the wires route around the screw stud. A tiny dab of glue can be used to keep the pod and cap together if it's an issue during install.
 - **0:53** This step is only for aligning the Z Endstop Pod, not for adjusting the height of the Z Joint at endstop trigger.
 - **1:37** These two cable covers are separate because the 9mm belt attached to this tensioner runs close to the extrusion. The gap between these cable covers should roughly match the gap in the tensioner where the 9mm toothed idler sits.
 - **2:16** The Z Endstop Pods will need to be installed with the mounting FHCS screws entering from the other side when installed on side A.  They are designed with this "symmetry" in mind -- also noted at 2:26.

<!-- ## Steps

### 1. Assemble and Install the Z Endstop Pods
 - Plug Z-69 into the connector on the Z Enstop Switch PCB.
 - Sandwich the Z Endstop Switch PCB between the Z Enstop Pod and Z Endstop Pod Cap, ensuring the wires route around the screw stud. A tiny dab of glue can be used to keep the pod and cap together if it's an issue during install.
 - Insert 2 M3 Roll-In Nuts into the inside slot of the lower side frame extrusion on side B as shown.
 - Loosely attach the Z Endstop Pod to the frame using 2 M3x20 FHCS. Don't tighten yet.
 - Slide the Z Endstop Pod under the endstop adjustment screw of Front Z Joint B.
 - Lower the Front Z Joint Bar to make sure the endstop adjustment screw presses the switch at the bend in the lever.
 - Tighten the Z Endstop Pod mounting screws.
 - Route the Z Endstop Pod wires through the extrusion slots as shown, installing cable covers as you go.
 - **Position the 25mm and 10mm along the front-facing slot of the lower rear extrusion such that the gap between them leaves room for the Z-axis belt that will come up from the tensioner**
 - Repeat this for all 4 Z Endstop pods using the cables listed above, making sure to check that the corresponding Z Endstop Adjustment Screw presses the switch at the bend in the lever. **The height of the endstop adjustment screws will be calibrated later**. -->

<!-- {: .note}
The Z Endstop Pods will need to be installed with the mounting FHCS screws entering from the other side when installed on side A. -->

#### Z Endstop Cable Location - Top View

```        
            Rear
      Z-70 ------ Z-71
        |          |
 Side A |          | Side B
        |          | 
      Z-68 ------ Z-69
            Front
```

## Interactive View
<div class="online_3d_viewer"
    model="https://media.githubusercontent.com/media/AutomatedLayers/VertigoMk1/main/docs/assets/3d/z_endstop.glb"
    backgroundcolor="244, 246, 250"
    environmentmap=
    "
    {{site.url}}/{{site.baseurl}}/assets/js/o3dv/envmaps/studio/px.png,
    {{site.url}}/{{site.baseurl}}/assets/js/o3dv/envmaps/studio/nx.png,
    {{site.url}}/{{site.baseurl}}/assets/js/o3dv/envmaps/studio/py.png,
    {{site.url}}/{{site.baseurl}}/assets/js/o3dv/envmaps/studio/ny.png,
    {{site.url}}/{{site.baseurl}}/assets/js/o3dv/envmaps/studio/pz.png,
    {{site.url}}/{{site.baseurl}}/assets/js/o3dv/envmaps/studio/nz.png
    "
    >
</div>

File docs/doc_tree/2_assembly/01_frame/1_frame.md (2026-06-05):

---
title: Frame
layout: assembly
parent: Assembly Guide
nav_order: 1
---

# Frame



## Materials

| Hardware                         | Qty |
|:---------------------------------|:-- -|
| Extrusion 2020-370-TPW           | 9   |
| Extrusion 2020-500-LCP-RCP-AH335 | 2   |
| Extrusion 2020-120-RTP-LCP       | 2   |
| Extrusion 2020-460-RTP-AH56-AV80 | 2   |
| Extrusion 2020-325-RTP-LCP       | 2   |
| M5x80 Threaded Rod               | 2   |
| M5x16 BHSC                       | 20  |

| Printed Parts                    | Qty |
|:---------------------------------|:-- -|
| <a href="https://github.com/AutomatedLayers/VertigoMk1/blob/main/hardware/STL/01%20Frame/Frame%20Post%20Connector%20-%20Q2%20(LDO%20Profile).STL" target="_blank">Frame Post Connector</a> | 2   |
| <a href="https://github.com/AutomatedLayers/VertigoMk1/blob/main/hardware/STL/00%20Tools/Frame%20Rear%20Bar%20Alignment%20Tool.STL" target="_blank">Frame Rear Bar Alignment Tool</a> | 1   |

{: .note}
> Guidance on reading Misumi extrusion part numbers:
> - 2020-# = 20mmx20mm aluminum extrusion with length #mm
> - TPW = tapped both ends
> - RTP/LTP = tapped one end
> - LCP/RCP = criss-cross through-holes 10mm from the end
> - AV# = vertical through-hole #mm from the end
> - AH# = horizontal through-hole #mm from the end

## Animated Assembly
<iframe style='width:100%; height:621px;' src="https://www.youtube.com/embed/UhqsCeh7ScM?si=IBMXTUi_TiNwXbuP" title="YouTube video player" frameborder="0" allow="accelerometer; autoplay; clipboard-write; encrypted-media; gyroscope; picture-in-picture; web-share" referrerpolicy="strict-origin-when-cross-origin" allowfullscreen></iframe>

## Assembly Notes

{: .note}
There are two versions of the printed part "Frame Post Connector": one for LDO extrusions and one for Misumi.

{: .note}
This works best on a granite surface or the flattest surface you've got. The use of a machinist's square or dial guage is highly recommended to ensure squareness.

- **0:08** Leave a ~3mm gap under the head of these M5x20 BHCS. The head needs to slide into the slot of the adjoining extrusion.
- **0:20** This label is wrong. It should show "Extrusion 2020-325-RTP-LCP." It is used as a reference for locating the front part of the gantry extrusion.
- **0:56** The M5x80 Threaded Rod should bottom out at about 16mm into the top (short) extrusion. Don't screw it in more than 16mm. The minimum is 9mm. 
  - Here, it may be useful -- but not necessary -- to use an Extrusion 2020-370-TPW on top of the long horizontal extrusion, butted up against the front vertical extrusion to make a mark where the frame post connector should end when tightened.
  

- **1:10** Extrusion 2020-370-TPW is used as a reference for locating the top part of the lower rear vertical extrusion. 
- **1:20** The upper extrusion is also 2020-370-TPW.
- **1:43** Extrusions are all 2020-370-TPW.

<!-- ## Steps -->
<!-- ### 1. Assemble the right and left sides of the frame first
 - Screw the M5x16 button heads into the tapped holes on the ends of the extrusions (that have them) leaving a 2.5mm gap.
 - Slide the joining extrusions onto the button heads. Tighten through the through-hole.
 - See the video to use extrusions as guides for ensuring squareness and alignment.
 - Make sure the cutout in the printed Frame Post Connectors are facing out.

### 2. Attach the sides together
 - Attach the bottom and top front extrusions .
 - Attach the rear extrusion using the alignment tools.
 - Attach the rear top extrusion. -->

{: .important}
 At this point, you really want to make sure your frame is square. Measure and make adjustments as needed. The diagonals for the top and bottom square should measure 523.3mm (+/-1).

## Interactive View
<div class="online_3d_viewer"
    model="https://media.githubusercontent.com/media/AutomatedLayers/VertigoMk1/main/docs/assets/3d/frame.glb"
    backgroundcolor="244, 246, 250"
    camera=
    "
    -0.014962905975541837, 0.39473399804174625, 0.9165612533280376,
    -0.013882773306938854, 0.41454617159466195, -0.0347976522736765,
    0, 1, 0
    "
    environmentmap=
    "
    {{site.url}}/{{site.baseurl}}/assets/js/o3dv/envmaps/studio/px.png,
    {{site.url}}/{{site.baseurl}}/assets/js/o3dv/envmaps/studio/nx.png,
    {{site.url}}/{{site.baseurl}}/assets/js/o3dv/envmaps/studio/py.png,
    {{site.url}}/{{site.baseurl}}/assets/js/o3dv/envmaps/studio/ny.png,
    {{site.url}}/{{site.baseurl}}/assets/js/o3dv/envmaps/studio/pz.png,
    {{site.url}}/{{site.baseurl}}/assets/js/o3dv/envmaps/studio/nz.png
    "
    >
</div>

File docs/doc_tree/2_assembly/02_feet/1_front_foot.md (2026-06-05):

---
title: Front Foot
layout: assembly
parent: Feet
nav_order: 1
---

# Front Foot


## Materials

| Hardware (for one foot)                   | Qty |   
|:------------------------------------------|:-- -|
| Gates GT2 20T Idler Pulley - 9mm Belt     | 1   |
| M8 Swivel Foot                            | 1   |
| M8 Hex Nut                                | 1   |
| M5x60 BHSC                                | 3   |
| M5x35 BHSC                                | 2   |
| M5x30 BHSC                                | 2   |
| M5 Hex Nut                                | 4   |
| M5 Roll-In Nut                            | 3   |
| M3x35 SHSC                                | 2   |
| M3x45 SHSC                                | 1   |
| M3 Hex Nut                                | 2   |
| Piece of Filament (1 piece is enough for both feet)| 100mm|

| Printed Parts                    | Qty |
|:---------------------------------|:-- -|
| <a href="https://github.com/AutomatedLayers/VertigoMk1/blob/main/hardware/STL/02%20Feet/Front%20Feet/Foot%20Front%20A%20Base.stl" target="_blank">Foot Front A Base</a> | 1   |
| <a href="https://github.com/AutomatedLayers/VertigoMk1/blob/main/hardware/STL/02%20Feet/Front%20Feet/Foot%20Front%20A%20Frame.stl" target="_blank">Foot Front A Frame</a> | 1   |
| <a href="https://github.com/AutomatedLayers/VertigoMk1/blob/main/hardware/STL/02%20Feet/Front%20Feet/Foot%20Front%20B%20Base.stl" target="_blank">Foot Front B Base</a> | 1   |
| <a href="https://github.com/AutomatedLayers/VertigoMk1/blob/main/hardware/STL/02%20Feet/Front%20Feet/Foot%20Front%20B%20Frame.stl" target="_blank">Foot Front B Frame</a> | 1   |
| <a href="https://github.com/AutomatedLayers/VertigoMk1/blob/main/hardware/STL/02%20Feet/Front%20Feet/Foot%20Front%20Replaceable%20Thread%20Plug%20-%20Q2.stl" target="_blank">Foot Front Replaceable Thread Plug</a> | 2   |
| <a href="https://github.com/AutomatedLayers/VertigoMk1/blob/main/hardware/STL/02%20Feet/All%20Feet/Foot%20Replaceable%20Thread%20Plug%20Retainer%20-%20Q4.stl" target="_blank">Foot Replaceable Thread Plug Retainer</a> | 2   |
| <a href="https://github.com/AutomatedLayers/VertigoMk1/blob/main/hardware/STL/02%20Feet/All%20Feet/Foot%20Height%20Knob%20-%20Accent%20-%20Q4.stl" target="_blank">Foot Height Knob</a> | 2   |
| <a href="https://github.com/AutomatedLayers/VertigoMk1/blob/main/hardware/STL/02%20Feet/All%20Feet/Foot%20Height%20Knob%20Cap%20-%20Accent%20-%20Q4.stl" target="_blank">Foot Height Knob Cap</a> | 2   |
| <a href="https://github.com/AutomatedLayers/VertigoMk1/blob/main/hardware/STL/02%20Feet/All%20Feet/Foot%20Z%20Tensioner%20-%20Accent%20-%20Q4.stl" target="_blank">Foot Z Tensioner</a> | 2   |
| <a href="https://github.com/AutomatedLayers/VertigoMk1/blob/main/hardware/STL/02%20Feet/All%20Feet/Foot%20Z%20Tensioner%20Knob%20-%20Accent%20-%20Q4.stl" target="_blank">Foot Z Tensioner Knob</a> | 2   |
| <a href="https://github.com/AutomatedLayers/VertigoMk1/blob/main/hardware/STL/00%20Tools/Front%20Foot%20Roll-In%20Nut%20Alignment%20Tool.STL" target="_blank">Front Foot Roll-In Nut Alignment Tool</a> | 1   |

## Animated Assembly
<iframe style='width:100%; height:621px;' src="https://www.youtube.com/embed/VdCMrKXNhDQ?si=9J2D0eltRY8zbf2H" title="YouTube video player" frameborder="0" allow="accelerometer; autoplay; clipboard-write; encrypted-media; gyroscope; picture-in-picture; web-share" referrerpolicy="strict-origin-when-cross-origin" allowfullscreen></iframe>

## Assembly Notes
<!-- ## Steps
### 1. Attach the Foot Housing to the Frame
 - Flip the printer frame upside down.
 - Place the 3 M5 Roll-In Nuts into the extrusion slots.
 - Use the Front Foot Roll-In Nut Alignment Tool to align the M5 Roll-In Nuts.
 - Drop the 2 M3 Hex Nuts into their slots in the Front Foot Frame.
 - Use pieces of filament to keep the M3 Hex Nuts in place.
 - Slide the 2 M5 Hex Nuts into their slots.
 - Attach the Foot Front Frame to the frame with 2 M5x35 BHCS.
 - Use two M5x60 BHCS to attach the Foot Front Base to the frame.
 - Use two M3x35 SHCS to secure the Foot Front Base to the frame.

### 2. Attach the Swivel Foot
 - Slide the Foot Height Knob onto the Swivel foot, and make sure it fits over the hex nut.
 - Screw the Foot Height Knob Cap onto the M8 thread to retain the Height Knob.
 - Place the M8 Hex Nut into the Replaceable Thread Plug.
 - Slide the Thread Plug Retainer onto the swivel foot.
 - Screw the Replaceable Thread Plug onto the swivel foot.
 - Align the notch on the Thread Plug Retainer with the hole on the front of the Foot Front Base.
 - Slide the Swivel Foot Assembly into the hole in the Foot Front Base.
 - Screw the M3x45 SHCS into the Foot Front Base to lock the Swivel Foot assembly in place.

### 3. Assemble the Tensioner -->

 - **1:35** See the note on the [Feet Tab]({{site.url}}/{{site.baseurl}}/doc_tree/2_assembly/02_feet/0_foot_assy.html). [Glue]({{site.url}}/{{site.baseurl}}/doc_tree/2_assembly/assembly.html#tools#:~:text=Cyanoacrylate%20Gel) may be applied to the threads just above the Height Knob where the Height Knob Cap will sit when screwed down.
 - **1:59** Skip the glue & threadlocker on this one; it's adjustable.
 - **2:06** Front view of the notch alignment

 - **2:26** Threadlocker can go on the vertical M5x30 BHCS ~3mm from the head.
 - **2:46** Tension Wheel (Tensioner Knob) does **not** actually need to "fit freely"; as long as it can be rotated by hand, it's good.
 - **2:55** An update was made to the [Foot Z Tensioner](https://github.com/AutomatedLayers/VertigoMk1/blob/main/hardware/STL/02%20Feet/All%20Feet/Foot%20Z%20Tensioner%20-%20Accent%20-%20Q4.stl) to place a line that should line up with the lip of the inside edge of the tensioner pocket when the tensioner is at the right starting point. <br>

 - **3:05** Removable for tensioning, no threadlocker

<!--
 - Place an M5 Hex Nut in the Z Tensioner Knob and slide the knob under the Foot Front Frame.
 - Place an M5 Hex Nut under the Z Tensioner and screw an M5x30 BHCS through the Z Tensioner and Nut.
 - Screw an M5x30 BHCS through the Z Tensioner and GT2 Idler Pulley - 9mmm.
 - Rotate the Z Tensioner Knob to screw the Z Tensioner down, aligning the bottom edge of the notch line in the tensioner with the lip of its pocket in the Foot Front Frame.
 - Screw the M5x60 BHCS through the Foot Rear Base, Z Tensioner Knob, and Foot Frame into the frame. -->

## Interactive View
<div class="online_3d_viewer"
    model="https://media.githubusercontent.com/media/AutomatedLayers/VertigoMk1/main/docs/assets/3d/front_foot.glb"
    backgroundcolor="244, 246, 250"
    environmentmap=
    "
    {{site.url}}/{{site.baseurl}}/assets/js/o3dv/envmaps/studio/px.png,
    {{site.url}}/{{site.baseurl}}/assets/js/o3dv/envmaps/studio/nx.png,
    {{site.url}}/{{site.baseurl}}/assets/js/o3dv/envmaps/studio/py.png,
    {{site.url}}/{{site.baseurl}}/assets/js/o3dv/envmaps/studio/ny.png,
    {{site.url}}/{{site.baseurl}}/assets/js/o3dv/envmaps/studio/pz.png,
    {{site.url}}/{{site.baseurl}}/assets/js/o3dv/envmaps/studio/nz.png
    "
    >
</div>

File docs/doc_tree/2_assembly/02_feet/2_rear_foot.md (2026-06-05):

---
title: Rear Foot
layout: assembly
parent: Feet
nav_order: 2
---

# Rear Foot


## Materials

| Hardware (for one foot)                   | Qty |
|:------------------------------------------|:-- -|
| Gates GT2 20T Idler Pulley - 9mm Belt     | 1   |
| M8 Swivel Foot                            | 1   |
| M8 Hex Nut                                | 1   |
| M5x60 BHSC                                | 3   |
| M5x35 BHSC                                | 1   |
| M5x30 BHSC                                | 2   |
| M5 Hex Nut                                | 2   |
| M5 T-Nut                                  | 3   |
| M3x45 SHSC                                | 1   |
| M3x20 SHSC                                | 1   |

| Printed Parts                    | Qty |
|:---------------------------------|:-- -|
| <a href="https://github.com/AutomatedLayers/VertigoMk1/blob/main/hardware/STL/02%20Feet/Rear%20Feet/Foot%20Rear%20A%20Base.stl" target="_blank">Foot Rear A Base</a> | 1   |
| <a href="https://github.com/AutomatedLayers/VertigoMk1/blob/main/hardware/STL/02%20Feet/Rear%20Feet/Foot%20Rear%20A%20Frame.stl" target="_blank">Foot Rear A Frame</a> | 1   |
| <a href="https://github.com/AutomatedLayers/VertigoMk1/blob/main/hardware/STL/02%20Feet/Rear%20Feet/Foot%20Rear%20A%20Logo%20Nugget%20-%20Accent%20-%20Multi.stl" target="_blank">Foot Rear A Logo Nugget</a> | 1   |
| <a href="https://github.com/AutomatedLayers/VertigoMk1/blob/main/hardware/STL/02%20Feet/Rear%20Feet/Foot%20Rear%20B%20Base.stl" target="_blank">Foot Rear B Base</a> | 1   |
| <a href="https://github.com/AutomatedLayers/VertigoMk1/blob/main/hardware/STL/02%20Feet/Rear%20Feet/Foot%20Rear%20B%20Frame.stl" target="_blank">Foot Rear B Frame</a> | 1   |
| <a href="https://github.com/AutomatedLayers/VertigoMk1/blob/main/hardware/STL/02%20Feet/Rear%20Feet/Foot%20Rear%20B%20Logo%20Nugget%20-%20Accent%20-%20Multi.stl" target="_blank">Foot Rear B Logo Nugget</a> | 1   |
| <a href="https://github.com/AutomatedLayers/VertigoMk1/blob/main/hardware/STL/02%20Feet/Rear%20Feet/Foot%20Rear%20Replaceable%20Thread%20Plug%20-%20Q2.stl" target="_blank">Foot Rear Replaceable Thread Plug</a> | 2   |
| <a href="https://github.com/AutomatedLayers/VertigoMk1/blob/main/hardware/STL/02%20Feet/All%20Feet/Foot%20Replaceable%20Thread%20Plug%20Retainer%20-%20Q4.stl" target="_blank">Foot Replaceable Thread Plug Retainer</a> | 2   |
| <a href="https://github.com/AutomatedLayers/VertigoMk1/blob/main/hardware/STL/02%20Feet/All%20Feet/Foot%20Height%20Knob%20-%20Accent%20-%20Q4.stl" target="_blank">Foot Height Knob</a> | 2   |
| <a href="https://github.com/AutomatedLayers/VertigoMk1/blob/main/hardware/STL/02%20Feet/All%20Feet/Foot%20Height%20Knob%20Cap%20-%20Accent%20-%20Q4.stl" target="_blank">Foot Height Knob Cap</a> | 2   |
| <a href="https://github.com/AutomatedLayers/VertigoMk1/blob/main/hardware/STL/02%20Feet/All%20Feet/Foot%20Z%20Tensioner%20-%20Accent%20-%20Q4.stl" target="_blank">Foot Z Tensioner</a> | 2   |
| <a href="https://github.com/AutomatedLayers/VertigoMk1/blob/main/hardware/STL/02%20Feet/All%20Feet/Foot%20Z%20Tensioner%20Knob%20-%20Accent%20-%20Q4.stl" target="_blank">Foot Z Tensioner Knob</a> | 2   |
| <a href="https://github.com/AutomatedLayers/VertigoMk1/blob/main/hardware/STL/00%20Tools/Rear%20Foot%20Roll-In%20Nut%20Alignment%20Tool.STL" target="_blank">Rear Foot Roll-In Nut Alignment Tool</a> | 1   |

## Animated Assembly
<iframe style='width:100%; height:621px;' src="https://www.youtube.com/embed/Mb4JhPzpK9k?si=E7iLLehHYLY9Megw" title="YouTube video player" frameborder="0" allow="accelerometer; autoplay; clipboard-write; encrypted-media; gyroscope; picture-in-picture; web-share" referrerpolicy="strict-origin-when-cross-origin" allowfullscreen></iframe>

## Assembly Notes

<!-- ## Steps
### 1. Attach the Foot Housing to the Frame
 - Flip the printer frame upside down.
 - Place the 3 M5 Roll-In Nuts into the extrusion slots.
 - Use the Rear Foot Roll-In Nut Alignment Tool to align the M5 Roll-In Nuts.
 - Drop the M5 Hex Nut into its hole and slide it into the slot in the Foot Rear Frame.
 - Attach the Foot Rear Frame to the frame with an M5x35 BHCS.
 - Attach the Logo Nugget to the Foot Rear Base with an M3x20 SHCS.
 - Use two M5x60 BHCS to attach the Foot Rear Base to the frame.

### 2. Attach the Swivel Foot
 - Slide the Foot Height Knob onto the Swivel foot, and make sure it fits over the hex nut.
 - Screw the Foot Height Knob Cap onto the M8 thread to retain the Height Knob.
 - Place the M8 Hex Nut into the Replaceable Thread Plug.
 - Slide the Thread Plug Retainer onto the swivel foot.
 - Screw the Replaceable Thread Plug onto the swivel foot.
 - Align the notch on the Replaceable Thread Plug with the hole on the face of the Foot Rear Base.
 - Slide the Swivel Foot Assembly into the hole in the Foot Rear Base.
 - Screw the M3x45 SHCS into the Foot Rear Base to lock the Swivel Foot assembly in place.

### 3. Assemble the Tensioner -->

{: .note}
The notes regarding the Height Knob and Tensioner from the Front Foot assembly apply here as well.

 - **0:00** Remove any support material.
 - **2:14** Bottom view of the slot/hole alignment


<!-- Place an M5 Hex Nut in the Z Tensioner Knob and slide the knob under the Foot Rear Frame.
 - Place an M5 Hex Nut under the Z Tensioner and screw an M5x30 BHCS through the Z Tensioner and Nut.
 - Screw an M5x30 BHCS through the Z Tensioner and GT2 Idler Pulley - 9mmm.
 - Rotate the Z Tensioner Knob to screw the Z Tensioner down, aligning the bottom edge of the notch line in the tensioner with the lip of its pocket in the Foot Rear Frame.
 - Screw the M5x60 BHCS through the Foot Rear Base, Z Tensioner Knob, and Foot Frame into the frame. -->

## Interactive View
<div class="online_3d_viewer"
    model="https://media.githubusercontent.com/media/AutomatedLayers/VertigoMk1/main/docs/assets/3d/rear_foot.glb"
    backgroundcolor="244, 246, 250"
    environmentmap=
    "
    {{site.url}}/{{site.baseurl}}/assets/js/o3dv/envmaps/studio/px.png,
    {{site.url}}/{{site.baseurl}}/assets/js/o3dv/envmaps/studio/nx.png,
    {{site.url}}/{{site.baseurl}}/assets/js/o3dv/envmaps/studio/py.png,
    {{site.url}}/{{site.baseurl}}/assets/js/o3dv/envmaps/studio/ny.png,
    {{site.url}}/{{site.baseurl}}/assets/js/o3dv/envmaps/studio/pz.png,
    {{site.url}}/{{site.baseurl}}/assets/js/o3dv/envmaps/studio/nz.png
    "
    >
</div>

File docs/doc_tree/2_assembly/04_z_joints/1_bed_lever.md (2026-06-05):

---
title: Bed Lever
layout: assembly
parent: Z Joints
nav_order: 1
---

# Bed Lever


## Materials

{: .warning }
The channel magnet is **STRONG**, and also rather fragile. Use caution with ferrous metal nearby, especially the strike plate that goes with the lever. Also, be careful not to overtighten the magnet's mounting screws; it will fracture.

| Hardware                                  | Qty |   
|:------------------------------------------|:-- -|
| Channel Magnet - 40mm                     | 1   |
| Bar Magnet Striker - 40mm [attached to Channel Magnet] | 1   |
| (Dual Hook Tension) Spring - 4x25mm       | 2   |
| Tooling Ball                              | 1   |
| M5 Hex Nut                                | 1   |
| M5x10x1 Washer                            | 1   |
| M3x60 Dowel                               | 2   |
| M5x60 D-Shaft                             | 1   |
| M5x16 BHCS                                | 2   |
| M3x12 SHCS                                | 2   |
| M3x10 FHCS                                | 4   |
| M2x8 SHCS                                 | 6   |
| M5 Roll-In Nut                            | 2   |
| M3 Roll-In Nut                            | 2   |
| M3 Hex Nut                                | 2   |

| Printed Parts                    | Qty |
|:---------------------------------|:-- -|
| <a href="https://github.com/AutomatedLayers/VertigoMk1/blob/main/hardware/STL/03%20Z%20Joints/Front%20Z%20Joints/Bed%20Lever/Bed%20Lever%20Frame%20Mount%20-%20Generate%20Supp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" target="_blank">Bed Lever Frame Mount</a> | 1   |
| <a href="https://github.com/AutomatedLayers/VertigoMk1/blob/main/hardware/STL/03%20Z%20Joints/Front%20Z%20Joints/Bed%20Lever/Bed%20Lever.stl" target="_blank">Bed Lever</a> | 1   |

## Animated Assembly

{: .important}
>WIP notes: 
>- The video shows the Front Z Joints being assembled before the bed lever. Feedback has suggested it is easier to attach the bed lever to the extrusion first to center it, then to move on to the Z Joints

<iframe style='width:100%; height:621px;' src="https://www.youtube.com/embed/2lDIZEWfpks?si=Or_HjbJ9XdGpA31k&amp;start=168"  title="YouTube video player" frameborder="0" allow="accelerometer; autoplay; clipboard-write; encrypted-media; gyroscope; picture-in-picture; web-share" referrerpolicy="strict-origin-when-cross-origin" allowfullscreen></iframe>

## Assembly Notes

<!-- ### 1. Setup the Front Z Joint Bar

 - Flip the Front Z Joint Bar upside down.
 - Place 2 M3 Roll-In Nuts into the extrusion.
 - Place 2 M5 Roll-In Nuts on the outside of the M3 Roll-In Nuts.
 - Use the Bed Lever Frame Mount  to align the Roll-In Nuts. The whole assembly will be centered later on the extrusion.

### 2. Assemble the Bed Lever

 - Drop a dab of red Loctite on the Tooling Ball thread.
 - Place the M5x10x1 Washer on the Bed Lever and screw the Tooling Ball through the washer and lever into an M5 Hex Nut.
 - Use a cloth (optional) and pliers on the Tooling Ball shank to tighten it to the Bed Lever.
 - Push 2 M3x60 Dowels into the Bed Lever. These add to the rigidity of the lever.
 - Attach the Strike Plate to the lever using 2 M3x10 FHCS and 2 M3 Hex Nuts.
 - On each outer side of the Bed Lever Frame Mount, thread in an M2x8 SHCS until the end is flush with the inner face of the part.
 - On each inner side of the frame mount, attach a Tension Spring using an M2x8 SHCS. The heads of these screws should be flush with the innermost printed surface.
 - Position the Bed Lever  in the Frame Mount and push an M5x60 D-Shaft through both parts. The fit should be very snug in the lever.
 - In the Frame Mount, thread in 2 M3x12 SHCS until the ends are just visible in the D-Shaft slotted hole.
 - Place 2 M2x8 SHCS through the open end of the Torsion Springs and thread them into their holes in the Bed Lever, leveraging the Torsion Springs into the stretched position.
 - Open the lever and lock it in the open position using the 2 outer M2x8 SHCS.
  
### 3. Attach the Bed Lever to the Front Z Joint Bar -->

 - **3:38** Dowels are here to increase rigidity. They should not fall out once inserted, if they do, either adjust your shrinkage compensation or use a bit of glue if they're not too loose.
 - **3:51** Use some threadlocker on the M5 Hex Nut to secure the Tooling Ball.
 - **3:57** Tighten by the **shank only**.
 - **4:12** The shaft should be a **really snug fit** and will only go into the lever if the flat face is down.
 - **4:22** Use the M2 SHCS to leverage the spring's hook into position.

<!--
 - Place the Channel Magnet into the Bed Lever Frame Mount  and loosely fasten it to the extrusion with 2 M3x10 FHCS.
 - Screw 2 M5x16 BHCS loosely through the Bed Lever Frame Mount to the extrusion.
 - Slide the Bed Lever Assembly until it is centered on the extrusion. The edge of the Frame Mount should be ~118mm from the end of the extrusion.
 - Tighten the 2 M3x10 FHCS and 2 M5x16 BHCS to secure the assembly to the extrusion.
 - Hold open the Bed Lever and loosen the two M2x8 SHCS position locks.
 - **Carefully and Slowly** close the lever.
 - Screw in the M3x12 SHCS on Side A until the head is on the stopper.
 - Screw in the M3x12 SHCS on Side B until the screw just barely touches the M5x60 D-Shaft. -->

{: .important}
>**4:30** Make sure the lever is in closed position. Place a dab of glue on the fixed M3x12 SHCS and screw until the head touches the printed stud. Screw in the adjustable M3x12 SHCS until it just touches the D-Shaft. Check for any play in the bed lever by trying to rock it across an imaginary axis from the fixed M3x12 SHCS on Side A to the corner of the strike plate on Side B. If there is play when the lever is closed, make sure the adjustable M3 screw is not pushing on the D-shaft and that the magnet and strike plate are properly installed. Check that no pieces of metal or debris got stuck under the magnet. When the lever feels solid, remove the adjustable M3x12 SHCS, drop a dab of glue on its threads, and screw it back to where it was touching the D-Shaft now that you know what you're doing.
>
>

{: .warning}
**5:21** **Don't let the lever snap closed!** You could seriously injure a finger or break the magnet. 

{: .note} 
The lever is designed such that the magnet and strike plate -- installed at a slight angle -- create a line contact, analogous to 2 points. The fixed M3 screw provides a 3rd point contact. The lever is further constrained in Rz, X, and Y by the hinge. This means that the adjustable M3 screw on Side B is an overconstraint when the lever is closed. It is used to constrain the lever motion during the opening action that allows the bed to rotate vertically (hence Vertigo 😵‍💫). 

## Interactive View
<div class="online_3d_viewer"
    model="https://media.githubusercontent.com/media/AutomatedLayers/VertigoMk1/main/docs/assets/3d/bed_lever.glb"
    backgroundcolor="244, 246, 250"
    environmentmap=
    "
    {{site.url}}/{{site.baseurl}}/assets/js/o3dv/envmaps/studio/px.png,
    {{site.url}}/{{site.baseurl}}/assets/js/o3dv/envmaps/studio/nx.png,
    {{site.url}}/{{site.baseurl}}/assets/js/o3dv/envmaps/studio/py.png,
    {{site.url}}/{{site.baseurl}}/assets/js/o3dv/envmaps/studio/ny.png,
    {{site.url}}/{{site.baseurl}}/assets/js/o3dv/envmaps/studio/pz.png,
    {{site.url}}/{{site.baseurl}}/assets/js/o3dv/envmaps/studio/nz.png
    "
    >
</div>

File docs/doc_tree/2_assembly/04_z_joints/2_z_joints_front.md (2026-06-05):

---
title: Front Z Joints
layout: assembly
parent: Z Joints
nav_order: 2
---

# Front Z Joints


## Materials

| Hardware (for each side)                  | Qty |   
|:------------------------------------------|:-- -| 
| Extrusion 2020-320                        | 1   |
| M3x10Lx6W Hex Standoff (Coupling Hex Nut) | 2   |
| Spherical Bearing - GE5C                  | 1   |
| M5x20 BHCS                                | 1   | 
| M5x40 BHCS                                | 1   | 
| M3x16 SHCS                                | 4   | 
| M3x25 SHCS                                | 4   | 
| M3x35 SHCS                                | 2   | 
| M3x40 SHCS                                | 2   | 
| M3x5.7 Brass Insert                       | 2   | 
| M3x4.3 Brass Insert (4.5)                 | 2   | 
| M5 Roll-In Nut                            | 1   |
| [***Side B Only** M3x10 SHCS]              | [1] | 

| Printed Parts                    | Qty |
|:---------------------------------|:-- -|
| <a href="https://github.com/AutomatedLayers/VertigoMk1/blob/main/hardware/STL/03%20Z%20Joints/Belt%20Clamps/Belt%20Clamp%20Bottom%20-%20Accent%20-%20Q4.stl" target="_blank">Belt Clamp Bottom</a> | 2   |
| <a href="https://github.com/AutomatedLayers/VertigoMk1/blob/main/hardware/STL/03%20Z%20Joints/Belt%20Clamps/Belt%20Clamp%20Top%20-%20Accent%20-%20Q4.stl" target="_blank">Belt Clamp Top</a> | 2   |
| <a href="https://github.com/AutomatedLayers/VertigoMk1/blob/main/hardware/STL/03%20Z%20Joints/Front%20Z%20Joints/Front%20Joint%20-%20Spherical%20Bearing%20Block%20-%20Accent%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" target="_blank">Spherical Bearing Block</a> | 2   |
| <a href="https://github.com/AutomatedLayers/VertigoMk1/blob/main/hardware/STL/03%20Z%20Joints/Front%20Z%20Joints/Front%20Joint%20A%20-%20Carriage%20Block%20-%20Multi.stl" target="_blank">Front Joint A - Carriage Block</a> | 1   |
| <a href="https://github.com/AutomatedLayers/VertigoMk1/blob/main/hardware/STL/03%20Z%20Joints/Front%20Z%20Joints/Front%20Joint%20A%20-%20Endstop%20Adjustment.stl" target="_blank">Front Joint A - Endstop Adjustment</a> | 1   |
| <a href="https://github.com/AutomatedLayers/VertigoMk1/blob/main/hardware/STL/03%20Z%20Joints/Front%20Z%20Joints/Front%20Joint%20A%20-%20Middle%20Support.stl" target="_blank">Front Joint A - Middle Support</a> | 1   |
| <a href="https://github.com/AutomatedLayers/VertigoMk1/blob/main/hardware/STL/03%20Z%20Joints/Front%20Z%20Joints/Front%20Joint%20A%20-%20Rear%20Cover.stl" target="_blank">Front Joint A - Rear Cover</a> | 1   |
| <a href="https://github.com/AutomatedLayers/VertigoMk1/blob/main/hardware/STL/03%20Z%20Joints/Front%20Z%20Joints/Front%20Joint%20B%20-%20Carriage%20Block%20-%20Multi.stl" target="_blank">Front Joint B - Carriage Block</a> | 1   |
| <a href="https://github.com/AutomatedLayers/VertigoMk1/blob/main/hardware/STL/03%20Z%20Joints/Front%20Z%20Joints/Front%20Joint%20B%20-%20Endstop%20Adjustment.stl" target="_blank">Front Joint B - Endstop Adjustment</a> | 1   |
| <a href="https://github.com/AutomatedLayers/VertigoMk1/blob/main/hardware/STL/03%20Z%20Joints/Front%20Z%20Joints/Front%20Joint%20B%20-%20Middle%20Support.stl" target="_blank">Front Joint B - Middle Support</a> | 1   |
| <a href="https://github.com/AutomatedLayers/VertigoMk1/blob/main/hardware/STL/03%20Z%20Joints/Front%20Z%20Joints/Front%20Joint%20B%20-%20Rear%20Cover.stl" target="_blank">Front Joint B - Rear Cover</a> | 1   |

## Animated Assembly

<iframe style='width:100%; height:621px;' src="https://www.youtube.com/embed/2lDIZEWfpks?si=Or_HjbJ9XdGpA31k"  title="YouTube video player" frameborder="0" allow="accelerometer; autoplay; clipboard-write; encrypted-media; gyroscope; picture-in-picture; web-share" referrerpolicy="strict-origin-when-cross-origin" allowfullscreen></iframe>

## Assembly Notes

 - **1:10** Both The M5x20 BHCS and M3x10 SHCS thread into plastic. They will be used to adjust the height of the Z Joints when the endstop and safety switch are triggered, respectively. Skip the glue until that calibration is done. Side A has no M3x10 SHCS safety switch position screw, so the Endstop Adjustment printed part looks a bit different on side A and B.
 - **2:40** If it's tricky to slide the Z Joints into the extrusion with the roll-in nuts attached, just unscrew them and insert them into the extrusion first.
 - **2:43** This can be dialed in later when the Front Z Joints are attached to the rails.

<!-- ### 1. Assemble Front Z Joint
 - Press in 2 M3x5.7 Brass Inserts to the Front Joint B Carriage Block.
 - Slide the M3x10 Coupling Nut into the rear slot in the Front Joint B Carriage Block.
 - Push in 2 M3x25 SHCS as shown.
 - Use 2 M3x25 SHCS to attach the Front Joint B Rear Cover.
 - Press in 2 M3x4.3 Brass Inserts to the Front Joint B Endstop Adjustment.
 - Thread a M5x20 BHCS into the Front Joint B Endstop Adjustment. The proper location of this screw will be adjusted later.
 - **[*Side B Only** Thread a M3x10 SHCS into the Front Joint B Endstop Adjustment. The proper location of this screw will be adjusted later**]**.
 - Slide the Front Joint B Middle Support into place and fasten it with 2 M3x40 SHCS.
 - Slide the M3x10 Coupling Nut into the front slot in the Front Joint B Carriage Block.
 - Push in 2 M3x35 SHCS as shown.
 - Use 2 M3x16 SHCS to attach a belt clamp to the top and bottom of the Front Joint B Carriage Block.
 - Press the Spherical Bearing GE5C into the Front Joint Spherical Bearing Block.
 - Make sure the slot in the printed bearing block points toward the belt clamps.
 - Push an M5x40 BHCS through the spherical bearing and Z Joint, and thread it into an M5 Roll-In Nut but do not tighten.

### 2. Assemble Front Z Joint Bar
 - Repeat Step 1 for Front Z Joint A.
 - Slide the Z Joints onto either end of the Extrusion 2020-320 such that the roll-in nuts enter the extrusion slot.
 - Leave about 1mm on each side and snug the M5x40 BHCS but still do not tighten yet.
 - Attach the Front Z Joint Bar to the Z Axis Linear Carriages by first tightening the captive fasteners, then the outer fasteners.
 - Make sure the gaps are about even on both ends of the extrusion and that the Front Z Joint Bar slides freely up and down the Z Axis.
 - Finally you get to tighten the M5x40 BHCS . -->

## Interactive View
<div class="online_3d_viewer"
    model="https://media.githubusercontent.com/media/AutomatedLayers/VertigoMk1/main/docs/assets/3d/front_z_joints.glb"
    backgroundcolor="244, 246, 250"
    camera="
    0, 0.35460301851425213, 0.5353489231611536,
    0, 0.31849222391429477, 0.14661257197666216,
    0, 1, 0
    "
    environmentmap=
    "
    {{site.url}}/{{site.baseurl}}/assets/js/o3dv/envmaps/studio/px.png,
    {{site.url}}/{{site.baseurl}}/assets/js/o3dv/envmaps/studio/nx.png,
    {{site.url}}/{{site.baseurl}}/assets/js/o3dv/envmaps/studio/py.png,
    {{site.url}}/{{site.baseurl}}/assets/js/o3dv/envmaps/studio/ny.png,
    {{site.url}}/{{site.baseurl}}/assets/js/o3dv/envmaps/studio/pz.png,
    {{site.url}}/{{site.baseurl}}/assets/js/o3dv/envmaps/studio/nz.png
    "
    >
</div>

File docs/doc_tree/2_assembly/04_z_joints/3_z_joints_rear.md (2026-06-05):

---
title: Rear Z Joints
layout: assembly
parent: Z Joints
nav_order: 3
---

# Rear Z Joints


## Materials

| Hardware (for each side)                  | Qty |   
|:------------------------------------------|:-- -| 
| M3x10Lx6W Hex Standoff (Coupling Hex Nut) | 2   |
| M3x60 Dowel                               | 2   |
| M5x20 BHCS                                | 1   | 
| M3x16 SHCS                                | 7   | 
| M3x25 SHCS                                | 4   | 
| M3x40 SHCS                                | 1   | 
| M3x45 SHCS                                | 2   | 
| M3x4.3 Brass Insert (4.5)                 | 2   | 
| M3 Hex Nut                                | 4   |

| Printed Parts                    | Qty |
|:---------------------------------|:-- -|
| <a href="https://github.com/AutomatedLayers/VertigoMk1/blob/main/hardware/STL/03%20Z%20Joints/Belt%20Clamps/Belt%20Clamp%20Bottom_9mm%20-%20Accent%20-%20Q4.stl" target="_blank">Belt Clamp Bottom</a> | 2   |
| <a href="https://github.com/AutomatedLayers/VertigoMk1/blob/main/hardware/STL/03%20Z%20Joints/Belt%20Clamps/Belt%20Clamp%20Top_9mm%20-%20Accent%20-%20Q4.stl" target="_blank">Belt Clamp Top</a> | 2   |
| <a href="https://github.com/AutomatedLayers/VertigoMk1/blob/main/hardware/STL/03%20Z%20Joints/Rear%20Z%20Joints/Rear%20Joint%20A%20-%20Carriage%20Block.stl" target="_blank">Rear Joint A - Carriage Block</a> | 1   |
| <a href="https://github.com/AutomatedLayers/VertigoMk1/blob/main/hardware/STL/03%20Z%20Joints/Rear%20Z%20Joints/Rear%20Joint%20A%20-%20Cup%20Block%20-%20Accent.stl" target="_blank">Rear Joint A - Cup Block</a> | 1   |
| <a href="https://github.com/AutomatedLayers/VertigoMk1/blob/main/hardware/STL/03%20Z%20Joints/Rear%20Z%20Joints/Rear%20Joint%20A%20-%20Dowel%20Cap.stl" target="_blank">Rear Joint A - Dowel Cap</a> | 1   |
| <a href="https://github.com/AutomatedLayers/VertigoMk1/blob/main/hardware/STL/03%20Z%20Joints/Rear%20Z%20Joints/Rear%20Joint%20A%20-%20Kinematic%20Slot%20Seatbelt%20L.stl" target="_blank">Rear Joint A - Kinematic Slot Seatbelt L</a> | 1   |
| <a href="https://github.com/AutomatedLayers/VertigoMk1/blob/main/hardware/STL/03%20Z%20Joints/Rear%20Z%20Joints/Rear%20Joint%20A%20-%20Kinematic%20Slot%20Seatbelt%20R.stl" target="_blank">Rear Joint A - Kinematic Slot Seatbelt R</a> | 1   |
| <a href="https://github.com/AutomatedLayers/VertigoMk1/blob/main/hardware/STL/03%20Z%20Joints/Rear%20Z%20Joints/Rear%20Joint%20B%20-%20Carriage%20Block.stl" target="_blank">Rear Joint B - Carriage Block</a> | 1   |
| <a href="https://github.com/AutomatedLayers/VertigoMk1/blob/main/hardware/STL/03%20Z%20Joints/Rear%20Z%20Joints/Rear%20Joint%20B%20-%20Cup%20Block%20-%20Accent.stl" target="_blank">Rear Joint B - Cup Block</a> | 1   |
| <a href="https://github.com/AutomatedLayers/VertigoMk1/blob/main/hardware/STL/03%20Z%20Joints/Rear%20Z%20Joints/Rear%20Joint%20B%20-%20Dowel%20Cap.stl" target="_blank">Rear Joint B - Dowel Cap</a> | 1   |
| <a href="https://github.com/AutomatedLayers/VertigoMk1/blob/main/hardware/STL/03%20Z%20Joints/Rear%20Z%20Joints/Rear%20Joint%20B%20-%20Kinematic%20Slot%20Seatbelt%20L.stl" target="_blank">Rear Joint B - Kinematic Slot Seatbelt L</a> | 1   |
| <a href="https://github.com/AutomatedLayers/VertigoMk1/blob/main/hardware/STL/03%20Z%20Joints/Rear%20Z%20Joints/Rear%20Joint%20B%20-%20Kinematic%20Slot%20Seatbelt%20R.stl" target="_blank">Rear Joint B - Kinematic Slot Seatbelt R</a> | 1   |
| <a href="https://github.com/AutomatedLayers/VertigoMk1/blob/main/hardware/STL/03%20Z%20Joints/Rear%20Z%20Joints/Rear%20Joint%20B%20-%20Seatbelt%20Lock%20A.stl" target="_blank">Rear Joint B - Seatbelt Lock A</a> | 1   |
| <a href="https://github.com/AutomatedLayers/VertigoMk1/blob/main/hardware/STL/03%20Z%20Joints/Rear%20Z%20Joints/Rear%20Joint%20B%20-%20Seatbelt%20Lock%20B.stl" target="_blank">Rear Joint B - Seatbelt Lock B</a> | 1   |

## Animated Assembly

<iframe style='width:100%; height:621px;' src="https://www.youtube.com/embed/KFYv_QmUbJs?si=4q1HuJLT3oKaKD9-" title="YouTube video player" frameborder="0" allow="accelerometer; autoplay; clipboard-write; encrypted-media; gyroscope; picture-in-picture; web-share" referrerpolicy="strict-origin-when-cross-origin" allowfullscreen></iframe>

## Assembly Notes

 - **1:46** The M5x20 BHCS threads into plastic and will be used to adjust the Z Joint when the endstop is triggered. Skip any glue until calibration.
 - **1:49** Dowels should be a tight press into the Dowel Caps.
 - **2:03** Don't use threadlocker or tighten these very much, they will be readjusted when the print bed is installed.

{: .important}
**2:19** The dowels should fit into cup block tightly and not wiggle at all. If they do, adjust the holes or scaling in your slicer and reprint parts as needed. For Rear Z Joint Side A: the kinematic seatbelt should slide along the dowels, but they should not be loose, like a snug slip fit. **You may apply a small amount of grease on the dowels on side A**. See note below for more info.

{: .note}
There are two tooling balls on the rear of the bed that will fit into the kinematic "seatbelts" in these rear Z Joints. Those together with the tooling ball on the Bed Lever form a [Kelvin kinematic coupling](https://en.wikipedia.org/wiki/Kinematic_coupling#Kelvin_Coupling). The concept in our design is that one DOF is constrained by the Bed Lever, two on the rear Z Joint A, and three on the rear Z Joint B. This is why side B gets the seatbelt locks and side A has a bit of travel along the dowels. 

<!-- ## Steps
### 1. Assemble Front Z Joint B
 - Slide the M3x10 Coupling Nut into the inner slot in the Rear Joint B Carriage Block printed part.
 - Push in 2 M3x25 SHCS as shown.
 - Drop in 2 M3 Hex Nuts to the slots on the top and bottom of the Rear Joint B Cub Block printed part.
 - Use 2 M3x25 SHCS to fasten the carriage block to the cup block.
 - Tighten a M3x40 SHCS through the carriage block into a M3 Hex Nut in the cup block.
 - Slide the M3x10 Coupling Nut into the outer slot in the Rear Joint B Carriage Block printed part. If it falls out, just remember to put it in before attaching the joint to the linear carrige.
 - Use 2 M3x16 SHCS to attach a belt clamp to the top and bottom of the Rear Joint B Carriage Block printed part.

### 2. Assemble Kinematic Seatbelt
 - Press in 2 M3x4.3 Brass Insert to the Rear Joint B Kinematic Slot Seatbelt R printed part.
 - Use 2 M3x16 SHCS to attach both sides of the kinematic seatbelt.
 - Thread a M5x20 BHCS into the Rear Joint B Dowel Cap printed part. The proper location of this screw will be adjusted later.
 - Press fit 2 M3x60 Dowels into the dowel cap and slide the dowels into the holes in the cup block.
 - Place an M3 Hex Nut in the pocket on cup block and hold the kinematic seatbelt over the nut in position.
 - Slide the dowels all the way through the cup block and seatbelt until the dowel cap touches the cup block.
 - Use an M3x16 SHCS to fix the dowel cap in place .

### 3. Attach Rear Z Joint to Linear Carriage
 - Push in 2 M3x45 SHCS to the cup block as shown.
 - Attach the Rear Z Joint to the rear linear carriage using the same procedure as the Front Z Joints; captive screws first, then outer screws.
 - **[ Side B Only** Loosen the M3 SHCS holding the dowel cap in place and slide on the two printed Seatbelt Locks as shown. Re-tighten the M3 SHCS **]**. -->

## Interactive View
<div class="online_3d_viewer"
    model="https://media.githubusercontent.com/media/AutomatedLayers/VertigoMk1/main/docs/assets/3d/rear_z_joints.glb"
    backgroundcolor="244, 246, 250"
    environmentmap=
    "
    {{site.url}}/{{site.baseurl}}/assets/js/o3dv/envmaps/studio/px.png,
    {{site.url}}/{{site.baseurl}}/assets/js/o3dv/envmaps/studio/nx.png,
    {{site.url}}/{{site.baseurl}}/assets/js/o3dv/envmaps/studio/py.png,
    {{site.url}}/{{site.baseurl}}/assets/js/o3dv/envmaps/studio/ny.png,
    {{site.url}}/{{site.baseurl}}/assets/js/o3dv/envmaps/studio/pz.png,
    {{site.url}}/{{site.baseurl}}/assets/js/o3dv/envmaps/studio/nz.png
    "
    >
</div>

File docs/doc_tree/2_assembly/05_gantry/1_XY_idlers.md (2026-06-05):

---
title: XY Idlers
layout: assembly
parent: Gantry
nav_order: 1
---

# XY Idlers



## Materials

| Hardware (for each side) | Qty | 
|:---|:----|
| Shoulder Screw - 25mmx5mm Shoulder - M5x9.5 Thread (M5x25mm)| 1 | 
| Bearing - F695 | 2 |
| M5x10x1 Washer | 2 |
| M5x10 BHCS | 1 | 
| M5x40 BHCS | 1 | 
| M5 Roll-In Nut | 3 |

| Printed Parts | Qty |
|:---|:----|
| <a href="https://github.com/AutomatedLayers/VertigoMk1/blob/main/hardware/STL/04%20XY%20Gantry/XY%20Idlers/XY%20Idler%20Block%20A.stl" target="_blank">XY Idler Block A</a> | 1  |
| <a href="https://github.com/AutomatedLayers/VertigoMk1/blob/main/hardware/STL/04%20XY%20Gantry/XY%20Idlers/XY%20Idler%20Block%20B.stl" target="_blank">XY Idler Block B</a> | 1 |
| <a href="https://github.com/AutomatedLayers/VertigoMk1/blob/main/hardware/STL/00%20Tools/Idler%20Bearing%20Tool.stl" target="_blank">Idler Bearing Tool</a> | 1 |

## Animated Assembly

<iframe style='width:100%; height:621px;' src="https://www.youtube.com/embed/eeNXnSOt2SM?si=kw3aZptvWjgTPuem" title="YouTube video player" frameborder="0" allow="accelerometer; autoplay; clipboard-write; encrypted-media; gyroscope; picture-in-picture; web-share" referrerpolicy="strict-origin-when-cross-origin" allowfullscreen></iframe>

## Assembly Notes

{: .important}
Don't overtighten the shoulder screw. The "smooth idler" bearings should spin freely.

<!-- ### 1. Assemble the XY Idler
 - Place 3 M5 Roll-In Nut in the frame as shown.
 - Combine the 2 M5x10x1 Washers and 2 F695 Bearings to create a "smooth idler pulley".
 - Use the XY Idler Tool to push the idler pulley into position and push the Shoulder Screw through the XY Idler Block and the idler pulley.
 - Secure the assembly to the frame using the M5x10 BHCS, M5x40 BHCS, and Shoulder Screw. **Don't overtighten the shoulder screw**. -->

## Interactive View

<div class="online_3d_viewer"
    model="https://media.githubusercontent.com/media/AutomatedLayers/VertigoMk1/main/docs/assets/3d/xy_idler.glb"
    backgroundcolor="244, 246, 250"
    camera="
    -0.10696708258892587, 0.5298596415005542, 0.16535934079488385,
    -0.19500021714581545, 0.5278500125141036, 0.16833345857979193, 
    0, 1, 0
    "
    environmentmap=
    "
    {{site.url}}/{{site.baseurl}}/assets/js/o3dv/envmaps/studio/px.png,
    {{site.url}}/{{site.baseurl}}/assets/js/o3dv/envmaps/studio/nx.png,
    {{site.url}}/{{site.baseurl}}/assets/js/o3dv/envmaps/studio/py.png,
    {{site.url}}/{{site.baseurl}}/assets/js/o3dv/envmaps/studio/ny.png,
    {{site.url}}/{{site.baseurl}}/assets/js/o3dv/envmaps/studio/pz.png,
    {{site.url}}/{{site.baseurl}}/assets/js/o3dv/envmaps/studio/nz.png
    "
    >
</div>

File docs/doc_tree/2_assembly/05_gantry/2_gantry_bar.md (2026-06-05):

---
title: Gantry Bar
layout: assembly
parent: Gantry
nav_order: 2
---

# Gantry Bar


## Materials

| Hardware - XY Joint (for each side) | Qty | 
|:---|:----|
| Shoulder Screw - 25mmx5mm Shoulder - M4x4.5 Thread (M4x25mm) | 2 | 
| Bearing - F695 | 2 |
| Gates GT2 Toothed Idler Pulley - 6mm Belt | 1 |
| M5x10x1 Washer | 2 |
| M5x7x1 Washer (Washer M5) | 2 |
| M5x20 BHCS | 1 | 
| M5x30 BHCS  [M5x35 BHCS for Side B] | 1 | 
| M3x30 SHCS | 1 | 
| M3x35 SHCS | 1 | 
| M3x12 FHCS | 4 | 
| M5 Roll-In Nut | 1 |
| M5 Hex Nut | 1 |
| M4 Hex Nut | 2 |
| M3x5.7 Brass Insert | 2 | 
| **Hardware - X Axis** | **Qty** | 
|:---------------------------------------------------|:----| 
| Extrusion 2010-370-Z5-ZA25-XB345 | 1 |
| MGN9H-300 Linear Guide | 1 |
| M3 Roll-In Nut | 7 |
| M3x8 SHCS | 7 |
| **Hardware - X Carriage Block** | **Qty** | 
|:---------------------------------------------------|:----|
| Magnet - 1/2in Countersunk | 4 |
| Magnet - 1/4in Countersunk | 2 |
| Makerbeam XL T-Nut | 2 |
| M3x8 SHCS | 1 |
| M3x30 SHCS | 2 |
| M3x16 SHCS | 2 |
| M3x8 FHCS | 4 |
| M3 Cap Nut (Acorn Nut) | 3 |
| M2x16 SHCS | 2 |
| M2x8 FHCS | 2 |
| M2 Hex Nut | 2 |

| Printed Parts | Qty |
|:---|:----|
| <a href="https://github.com/AutomatedLayers/VertigoMk1/blob/main/hardware/STL/04%20XY%20Gantry/XY%20Joints/XY%20Joint%20A%20-%20Bottom.stl" target="_blank">XY Joint A - Bottom</a> | 1  |
| <a href="https://github.com/AutomatedLayers/VertigoMk1/blob/main/hardware/STL/04%20XY%20Gantry/XY%20Joints/XY%20Joint%20A%20-%20Carriage.stl" target="_blank">XY Joint A - Carriage</a> | 1  |
| <a href="https://github.com/AutomatedLayers/VertigoMk1/blob/main/hardware/STL/04%20XY%20Gantry/XY%20Joints/XY%20Joint%20A%20-%20Top.stl" target="_blank">XY Joint A - Top</a> | 1  |
| <a href="https://github.com/AutomatedLayers/VertigoMk1/blob/main/hardware/STL/04%20XY%20Gantry/XY%20Joints/XY%20Joint%20B%20-%20Bottom.stl" target="_blank">XY Joint B - Bottom</a> | 1  |
| <a href="https://github.com/AutomatedLayers/VertigoMk1/blob/main/hardware/STL/04%20XY%20Gantry/XY%20Joints/XY%20Joint%20B%20-%20Carriage.stl" target="_blank">XY Joint B - Carriage</a> | 1  |
| <a href="https://github.com/AutomatedLayers/VertigoMk1/blob/main/hardware/STL/04%20XY%20Gantry/XY%20Joints/XY%20Joint%20B%20-%20Top.stl" target="_blank">XY Joint B - Top</a> | 1  |
| <a href="https://github.com/AutomatedLayers/VertigoMk1/blob/main/hardware/STL/04%20XY%20Gantry/XY%20Joints/XY%20Joint%20B%20-%20Endstop%20Block%20-%20Accent.stl" target="_blank">XY Joint B - Endstop Block</a> | 1  |

## Animated Assembly

<iframe style='width:100%; height:621px;' src="https://www.youtube.com/embed/W9qf38xfoFk?si=WkttvpxSy8tU3iub" title="YouTube video player" frameborder="0" allow="accelerometer; autoplay; clipboard-write; encrypted-media; gyroscope; picture-in-picture; web-share" referrerpolicy="strict-origin-when-cross-origin" allowfullscreen></iframe>

## Assembly Notes

 - **0:26** The M4 Nuts may not stay in their pockets, but they will be tightened into them soon, just don't lose them in the meantime.
 - **3:02** The assembly process is the same on this side but note from the video and the interactive model below that the locations of the toothed and smooth idlers are different. There is also no Endstop block on this side, so an M5x30 BHCS is used instead where the M5x35 BHCS is on side B.
 - **4:01** These M2 SHCS add a bit of rigidity. You can use glue when threading.
 - **4:30** See the magnet polarity information below. **Magnets are fragile! Do not over-tighten!**
 - **4:52** Installing these is easiest if each magnet is screwed down **one at a time**, otherwise they may attract, come loose from their pockets, snap together, and break. These are the magnets that should be used as a reference for others magnets, as described below. They are all the same polarity and relatively accessible. 

{: .important}
The Gantry Bar should slide easily along the full travel of the y-axis rails. If there are areas where you feel higher resistance than others, you may need to check the y-axis rail alignment, or possibly the alignment of the gantry extrusions on the frame.

<!-- ## Steps

### 1. Assemble XY Joint B
 - Insert an M3x5.7 Brass Insert and 2 M4 Hex Nuts into the XY Joint B - Bottom.
 - With the XY Joint B - Top, flipped upside down, insert one Shoulder Screw - 25mmx5mm Shoulder - M4x4.5 Thread through the XY Joint B - Top, an M5x7x1 Washer, a GT2 20T Toothed Idler, and another M5x7x1 Washer .
 - Insert another Shoulder Screw - 25mmx5mm Shoulder - M4x4.5 Thread through the XY Joint B - Top, an M5x10x1 Washer, an idler made from 2 Bearings - F695, and another M5x10x1 Washer.
 - Slide the XY Joint B - Bottom over the shoulder bolts and fasten the bolts to the M4 Hex Nuts.
 - Secure the top and bottom of the XY Joint B assembly with an M3x30 SHCS.
 - Insert an M3x5.7 Brass Insert into the XY Joint B - Carriage.
 - Join the XY Joint B - Carriage to the XY Joint B - Bottom along the box joints and fasten with an M3x35 SHCS.
 - Slide the Extrusion 2010-370-Z5-ZA25-XB345 into the XY Joint B assembly.
 - Place an M5 Roll-In Nut into the extrusion slot and use an allen wrench to align it with the hole nearest the end of the extrusion in the XY Joint B - Top.
 - Fasten the XY Joint B assembly to the extrusion with an M5x20 BHCS into the aligned roll-in nut.
 - Place an M5 Hex Nut in the XY Joint B - Carriage; place the Endstop Block into the XY Joint B with the flat side facing the extrusion, and secure the XY Joint B assembly to the extrusion with an M5x35 BHCS.
  -->
<!-- ### 2. Assemble XY Joint A -->

<!-- ### 3. Assemble and Install the Toolhead Carriage Block
 - Use 7 M3x8 SHCS and M3 Roll-In Nuts to install the MGN9H-300 Linear Guide, using the rail alignment tools.
 - Screw in 2 M2x16 SHCS to the Toolhead Carriage Block. These are only to increase rigidity.
 - Insert 3 M3 Cap Nuts into the top of the Toolhead Carriage Block.
 - Fasten the cap nuts to the assembly with an M3x8 SHCS in the rear and 2 M3x30 SHCS in the front.
 - Attach 2 Magnet-1/4in Countersunk to the Toolhead Carriage Block with 2 M2x8 FHCS and 2 M2 Hex Nuts. **FRAGILE! Don't over-tighten.**
   - **Note the magnet polarity before installation.**
   - Refer to the image below for polarity orientation, using the Magnet-1/2in Countersunk as the reference.
 - Loosely attach 2 Makerbeam XL T-Nuts to the Toolhead Carriage Block with 2 M3x16 SHCS.
 - Install the Toolhead Carriage Block assembly to the X-axis linear guide with 4 M3x8 FHCS, screwing each of them through a Magnet-1/2in Countersunk. This is easiest if each magnet is screwed down **ONE AT A TIME**, otherwise they may attract, come loose from their pockets, and break. -->

---
#### Magnet Polarity


<!-- ### 4. Attach the Gantry Bar (X-axis) to the Y-Axis Carriages
 - Make sure the M5 Button Heads attaching the XY Joints to the X-axis extrusion are slightly loose, but still in the nuts. A half turn CCW should do.
 - Use 4 M3x12 FHCS to attach each XY Joint to the y-axis guide carriages.
 - Re-tighten the M5 Button heads. -->

---
## Interactive View
<div class="online_3d_viewer"
    model="https://media.githubusercontent.com/media/AutomatedLayers/VertigoMk1/main/docs/assets/3d/gantry_bar.glb"
    backgroundcolor="244, 246, 250"
    camera="
    -0.16462540259653796, 0.6947175468039145, 0.3110573203211509,
    -0.02628018914711079, 0.5102572622046775, 0.03436689342229495,
    0, 1, 0
    "
    environmentmap=
    "
    {{site.url}}/{{site.baseurl}}/assets/js/o3dv/envmaps/studio/px.png,
    {{site.url}}/{{site.baseurl}}/assets/js/o3dv/envmaps/studio/nx.png,
    {{site.url}}/{{site.baseurl}}/assets/js/o3dv/envmaps/studio/py.png,
    {{site.url}}/{{site.baseurl}}/assets/js/o3dv/envmaps/studio/ny.png,
    {{site.url}}/{{site.baseurl}}/assets/js/o3dv/envmaps/studio/pz.png,
    {{site.url}}/{{site.baseurl}}/assets/js/o3dv/envmaps/studio/nz.png
    "
    >
</div>

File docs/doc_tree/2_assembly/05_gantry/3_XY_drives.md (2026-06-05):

---
title: XY Drives
layout: assembly
parent: Gantry
nav_order: 3
---

# XY Drives


## Materials

| Hardware (for each side) | Qty | 
|:---|:----|
| Stepper Motor - LDO-42STH48-2804AC | 1 |
| Shoulder Screw - 25mmx5mm Shoulder - M5x9.5 Thread (M5x25mm) | 2 |
| GT2 20T Timing Pulley - 6mm Belt | 1 |
| Bearing - F695 | 6 |
| M5 x 40 BHCS | 3 |
| M5x10x1 Washer | 6 |
| M5 Roll-In Nut | 5 |
| M3x40 SHCS | 4 |
| M3x30 SHCS | 4 |
| M3x5.7 Brass Insert | 3 | 

| Printed Parts | Qty |
|:---|:----|
| <a href="https://github.com/AutomatedLayers/VertigoMk1/blob/main/hardware/STL/04%20XY%20Gantry/XY%20Drives/XY%20Drive%20A%20Cam%20-%20Accent.stl" target="_blank">XY Drive A Cam</a> | 1  |
| <a href="https://github.com/AutomatedLayers/VertigoMk1/blob/main/hardware/STL/04%20XY%20Gantry/XY%20Drives/XY%20Drive%20A%20Cam%20Cap%20-%20Accent.stl" target="_blank">XY Drive A Cam Cap</a> | 1  |
| <a href="https://github.com/AutomatedLayers/VertigoMk1/blob/main/hardware/STL/04%20XY%20Gantry/XY%20Drives/XY%20Drive%20A%20Cam%20Slider%20-%20Accent.stl" target="_blank">XY Drive A Cam Slider</a> | 1  |
| <a href="https://github.com/AutomatedLayers/VertigoMk1/blob/main/hardware/STL/04%20XY%20Gantry/XY%20Drives/XY%20Drive%20A%20Lid.stl" target="_blank">(Optional) XY Drive A Lid</a> | 1  |
| <a href="https://github.com/AutomatedLayers/VertigoMk1/blob/main/hardware/STL/04%20XY%20Gantry/XY%20Drives/XY%20Drive%20B%20Cam%20-%20Accent.stl" target="_blank">XY Drive B Cam</a> | 1  |
| <a href="https://github.com/AutomatedLayers/VertigoMk1/blob/main/hardware/STL/04%20XY%20Gantry/XY%20Drives/XY%20Drive%20B%20Cam%20Cap%20-%20Accent.stl" target="_blank">XY Drive B Cam Cap</a> | 1  |
| <a href="https://github.com/AutomatedLayers/VertigoMk1/blob/main/hardware/STL/04%20XY%20Gantry/XY%20Drives/XY%20Drive%20B%20Cam%20Slider%20-%20Accent.stl" target="_blank">XY Drive B Cam Slider</a> | 1  |
| <a href="https://github.com/AutomatedLayers/VertigoMk1/blob/main/hardware/STL/04%20XY%20Gantry/XY%20Drives/XY%20Drive%20B%20Lid.stl" target="_blank">(Optional) XY Drive B Lid</a> | 1  |
| <a href="https://github.com/AutomatedLayers/VertigoMk1/blob/main/hardware/STL/04%20XY%20Gantry/XY%20Drives/XY%20Drive%20Housing%20A%20-%20Bottom.stl" target="_blank">XY Drive Housing A - Bottom</a> | 1  |
| <a href="https://github.com/AutomatedLayers/VertigoMk1/blob/main/hardware/STL/04%20XY%20Gantry/XY%20Drives/XY%20Drive%20Housing%20A%20-%20Top.stl" target="_blank">XY Drive Housing A - Top</a> | 1  |
| <a href="https://github.com/AutomatedLayers/VertigoMk1/blob/main/hardware/STL/04%20XY%20Gantry/XY%20Drives/XY%20Drive%20Housing%20B%20-%20Bottom.stl" target="_blank">XY Drive Housing B - Bottom</a> | 1  |
| <a href="https://github.com/AutomatedLayers/VertigoMk1/blob/main/hardware/STL/04%20XY%20Gantry/XY%20Drives/XY%20Drive%20Housing%20B%20-%20Top.stl" target="_blank">XY Drive Housing B - Top</a> | 1  |
| <a href="https://github.com/AutomatedLayers/VertigoMk1/blob/main/hardware/STL/04%20XY%20Gantry/XY%20Drives/XY%20Drive%20Clamp%20Plate%20-%20Q2%20-%20Accent.stl" target="_blank">XY Drive Clamp Plate</a> | 2  |
| <a href="https://github.com/AutomatedLayers/VertigoMk1/blob/main/hardware/STL/04%20XY%20Gantry/XY%20Drives/XY%20Drive%20Spacer%20-%20Q2%20-%20Accent.stl" target="_blank">XY Drive Spacer</a> | 2  |
| <a href="https://github.com/AutomatedLayers/VertigoMk1/blob/main/hardware/STL/00%20Tools/Pulley%20Offset%20Tool%20Side%20A.STL" target="_blank">Pulley Offset Tool Side A</a> | 1  |
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

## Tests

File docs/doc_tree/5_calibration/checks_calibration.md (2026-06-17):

---
title: Checks & Calibration
layout: default
nav_order: 5
---

# Checks & Calibration
At this point, ideally you have completed:
 - the Assembly Guide up to -- but not including -- the Enclosure section,
 - the Wiring Guide, having linked back and forth from the Z Endstops, Toolhead, and Electronics Backpack sections respectively,
 - the Firmware Setup, with the ability now to access your printer's Mainsail User Interface via web browser. 

Before you get printing, there are a few things left to 'check and calibrate'. Follow this guide in order and don't hesitate to reach out on [Discord](https://discord.gg/qCQRbnZ6) if you run into issues.

{: .note}
The **Config Reference** sections below refer to the lines in configuration files where the relevant pins, parameters, modules, and macros can be found. Unless an instruction says to 'FIRMWARE RESTART', simply save the config file you're working on without a restart and continue. These files can be edited directly from Mainsail in the Machine tab in the Navigation Sidebar.

{: .warning}
During this setup, you will move axes *manually* -- with your hands -- while the motors are disabled. **Manually moving connected steppers too quickly can generate current that can damage the electronics!** So go slow. 🐢

## Table of Contents

- [Fans](#fans)
- [Lights](#lights)
- [Endstops](#endstops)
- [Safety Switch](#safety-switch)
- [Stepper Movement](#stepper-movement)
- [Homing](#homing)
- [Axis Movement](#axis-movement)
- [Nozzle Cleaner Position](#nozzle-cleaner-position)
- [Filament Cutter Position](#filament-cutter-position)
- [Nozzle Probe](#nozzle-probe)
- [Force Sensors](#force-sensors)
- [Bed Scrape Test](#bed-scrape-test)
- [Heaters](#heaters)
- [Resonance Compensation](#resonance-compensation)
- [Bed Leveling (Z Tilt) Test](#bed-leveling-z-tilt-test)
- [Global Z Offset](#global-z-offset)
- [Camera Options](#camera-options)

## Fans

### PSU Fan
This fan is internal to the 24V DC PSU and should be on when internal temperature is high or power loads are high. It is not specified in the config.

### Electronics Backpack Fans 
[See important note here]({{site.url}}/{{site.baseurl}}/2_assembly/14_electronics_backpack/0_electronics_backpack.html#assembly-notes). These fans should be on when the power is on. The stock fans are not controllable, therefore they are not specified in the config. However, if you switch them out, you could control them manually via a `[generic_fan]` section or based on the M8P MCU temperature using a `[temperature_fan]` section in printer.cfg. If they are too loud or you want to control them, you can upgrade to 4-pin PC fans like these [Noctua 4020 PWM Fans](https://www.noctua.at/en/products/nf-a4x20-pwm#hero). Just pay attention to how the connectors are wired, and take a look at the [M8P V2 Pinout]({{site.url}}/{{site.baseurl}}/assets/images/m8pv2_pinout.webp).

### Camera Fan
The Camera Fan should always be on. It runs on the same circuit as the logo LED, both of which are connected directly to the 24V PSU output.

### Part Cooling Fan
The three part cooling fans in the Cowl operate together on the same circuit and are simply called 'fan' by klipper and can be controlled via the "Miscellaneous" panel in the Mainsail Dashboard.

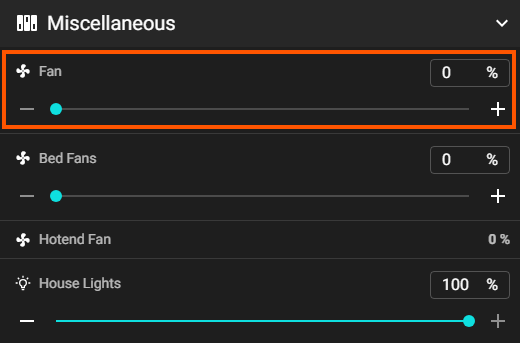
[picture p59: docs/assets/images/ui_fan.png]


#### Config Reference
```
printer.cfg
:
[fan] # Part Cooling
pin: toolhead:gpio21
```

### Hotend Fan
The Hotend Fan should turn on when the nozzle temperature exceeds the value defined in printer.cfg. This value is 45°C by default. We will tune the nozzle temperature control parameters later, but for now if you heat the nozzle to ~50°C, you should hear the fan spin up, feel a slight breeze on your finger behind the hotend, and see the %[fan power] value increaase in the "Miscellaneous" panel in the Mainsail Dashboard.

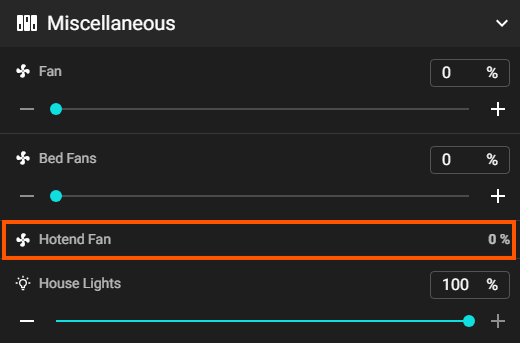
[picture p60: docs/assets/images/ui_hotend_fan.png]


#### Config Reference
```
printer.cfg
:
[heater_fan hotend_fan]
pin: toolhead:gpio13
heater: extruder
heater_temp: 45.0
```

### Bed Fans
The fans under the bed can help heat soak the build chamber when printing materials that like that envoronment. They also help cool the bed which helps release parts before scraping. The four fans operate together on the same circuit and are called 'bed fans' in the config and can be controlled via the "Miscellaneous" panel in the Mainsail Dashboard.

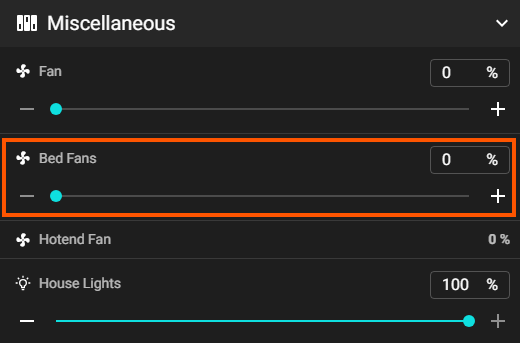
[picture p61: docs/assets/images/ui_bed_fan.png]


#### Config Reference
```
printer.cfg
:
[fan_generic bed_fans]
pin: PF7
```

## Lights

### VERTIGO LED
This LED at the top of the front of the printer is connected directly to the 24V PSU output, so it's not specified in the config file.

### Nozzle and Cowl Cap Logo LED
These are on the same circuit and get power from the 5V RGB output on the toolhead board, however they are wired to +5V and GND so they are not controllable or specified in the config. 
There was no more room to add pins to the Cowl pogo pin connector, so it would be difficult to change them to RGB.

### Enclosure Lights
These are called 'House Lights' in the config and controllable via the "Miscellaneous" panel in the Mainsail Dashboard.

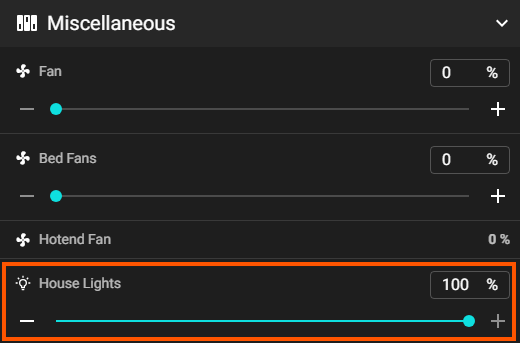
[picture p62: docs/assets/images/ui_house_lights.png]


#### Config Reference
```
printer.cfg
:
[led house_lights]
white_pin: PA4
initial_WHITE: 1.0
```

## Endstops

### Trigger Check
1. First make sure all motors are disabled, by power cycling or sending ```M84``` in the Console in Mainsail. 
2. With your hands, move the Gantry Bar to the center of the Y axis and the Toolhead to the center of the X axis. 
3. With the Bed Lever engaged, lift all four Z Joints several centimeters off the bottom of their travel. Make sure you can access and depress the switch on the X, Y, and four Z Endstops. 
4. Refresh the endstop states in Mainsail > Machine Tab > Endstops Panel > Refresh Button.
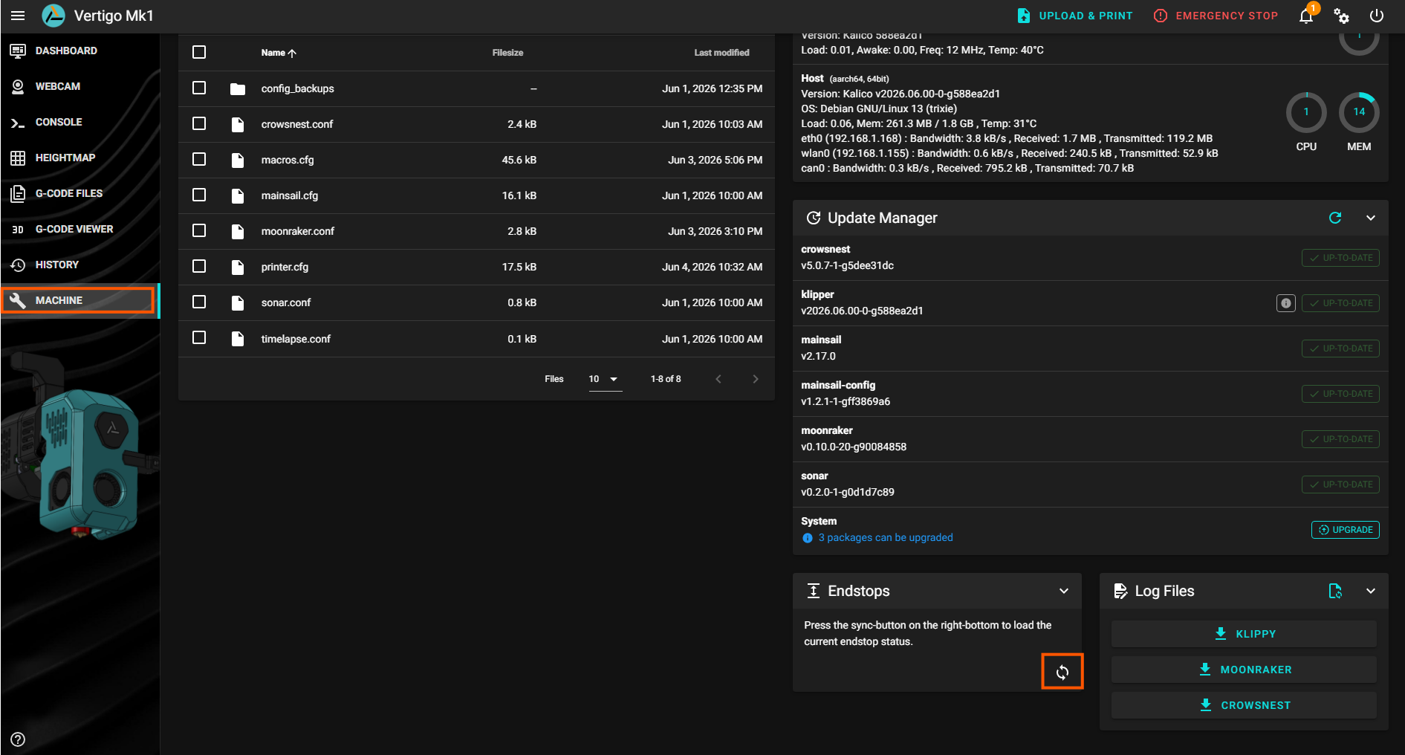
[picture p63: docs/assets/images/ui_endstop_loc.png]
>
5. The states should all be OPEN in the Endstops Panel.
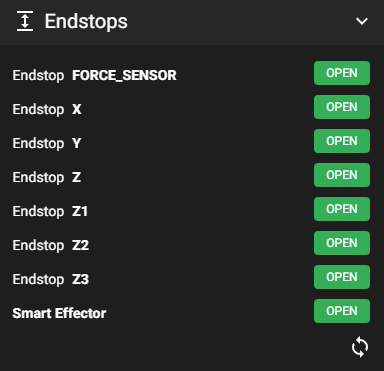
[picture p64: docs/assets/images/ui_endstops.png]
>
6. One-by-one, hold each endstop switch down while clicking the Refresh button to verify that each switch triggers and corresponds to the proper label in the Endstops panel. 
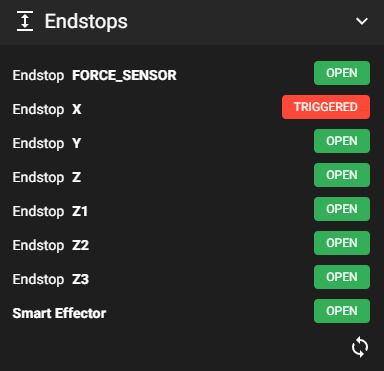
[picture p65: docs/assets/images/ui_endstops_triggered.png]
>

#### Z Endstop Location - Top View
```        
            Rear
       z2 -------- z3
        |          |
 Side A |          | Side B
        |          | 
        z -------- z1
            Front
```

### X/Y Endstop Calibration
The X and Y endstops for the gantry have no adjustment mechanism, so you must check that both trigger as expected, first by moving the toolhead to the right up against the X endstop, then by sliding the gantry bar back until XY Joint A triggers the Y Endstop. Use the Endstops Panel in Mainsail to verify.

#### Config Reference
```
printer.cfg
:
[stepper_x]
:
endstop_pin: ^toolhead:LIMIT_X

[stepper_y]
:
endstop_pin: ^!PC15
```

### Z Endstop Calibration
Each Z Joint has its own M5 BHCS adjustment screw. All Z Joints need to be "as close as can reliably trigger" to the bottom of the frame. A good way to do this is to:
1. Make sure the bed is roughly horizontal and that the bed wheels are resting on the ramp platform.
2. Unscrew the adjustment screws so that they don't trigger the switches when the Z Joints are at the bottom of travel (leaving ~1-5mm showing on the bottom).
3. Carefully push down the front Z Joint Bar so that the Bed Lever disengages and the Front Z Joints are touching the bottom of the frame.
4. Push down the Rear Z Joints so that they are touching the bottom of the frame. The front of the bed shouldd tilt up slightly.
5. Turn each adjustment screw until the corresponding endstop is TRIGGERED in the Endstops Panel. You can use the LED on the PCB as a guide. Give each screw an additional full turn, which equates to 0.8mm of depth. Assuming a worst case limit switch tolerance of +/- 0.1mm , this should give a gap of ~0.7-0.8mm between each Z Joint and the frame when the Endstops are triggered. **These endstops are not used for levelling the bed**. They are used to prepare the bed to be levelled by the probe and to be scraped after a print.

#### Config Reference
```
printer.cfg
:
[stepper_z]
:
endstop_pin: !PF4

[stepper_z1]
:
endstop_pin:!PF3

[stepper_z2]
:
endstop_pin: !PF2

[stepper_z3]
:
endstop_pin: !PF1
```

## Safety Switch
Most printers have the ability to plow the nozzle through the build plate and cause damage if things aren't calibrated for functioning properly. Because of the negative Z travel required for scraping the bed on the Vertigo, we have a few additional safety mechanisms. The Safety Switch prevents crashes at the top of the Front Z Axes, particularly in the event that the nozzle probe does not trigger or the front steppers are not disabled when scraping the bed. This switch will put klipper into an 'Emergency Shutdown' state, from which a firmware restart is required.

1. Hold the Bed Lever down and manually move the Front Z Joint Bar up until the tooling ball is above the bed contact plate.
2. Carefully let the Bed Lever close without snapping shut. 
3. Set the Safety Switch adjustment screw on Front Z Joint B so that it protrudes ~0-1mm.
4. Slowly raise the Front Z Joint Bar up until the carriages -- particularly on side B -- are ~1-2mm below the bottom of the horizontal gantry frame extrusions. 
5. Turn the Safety Switch adjustment screw until the switch triggers and the system shuts down. 
6. Click 'Firmware Restart' in the power menu at the top right of the Mainsail Dashboard.
7. Disengage the Bed Lever and slowly lower the Front Z Joint Bar until the tooling ball is below the bed contact plate and carefully let the Bed Lever close without snapping shut. The Bed Lever should be resting on the Bed Lever Striker, with the tooling ball below the bed contact plate. **Omitting this step can break your printer!**

#### Config Reference
```
printer.cfg
:
[gcode_button bed_safety_button]
pin: ^PC4

press_gcode:
  {action_emergency_stop("Impending Doom Averted!")}
```

## Stepper Movement
We'll use Klipper's STEPPER_BUZZ command to safely test whether the specified motor moves in the expected direction. This command will enable the stepper, rotate it both directions a small amount 10 times, then disable the stepper. If the stepper does not move in the expected manner, you must check the wiring and pinning of the connectors of the affected stepper.

#### Stepper Locations - Top View
```        
            Rear
        x          y 
        |          |   
       z2 -------- z3
        |          |
 Side A |          | Side B
        |          | 
        z -------- z1
            Front
```

### Z Stepper Test
The Z steppers will be tested in numerical order, front then rear. All Z Joints should move downward first.

1. With your hands, raise the Front Z Joint Bar so that the Bed Lever is just above the Bed Lever Striker. It should stay there without without drooping, but you can also hold it up if you need to. The tooling ball must still be below the bed contact plate.
2. In the config, stepper_z corresponds to the front stepper on side A. This is the one we will test first. In Mainsail > Dashboard Tab > Console Panel, type (or paste) the command: `STEPPER_BUZZ STEPPER=stepper_z`.
3. Repeat the test for stepper_z1: `STEPPER_BUZZ STEPPER=stepper_z1`.
4. Manually raise Rear Z Joint A and run the test: `STEPPER_BUZZ STEPPER=stepper_z2`.
5. Manually raise Rear Z Joint B and run the test: `STEPPER_BUZZ STEPPER=stepper_z3`.

#### Config Reference
```
printer.cfg
:
## Z0 Stepper - Front Left
[stepper_z]
dir_pin: PE5
step_pin: PE6
enable_pin: !PC14                        # active-low EN
rotation_distance: 40
gear_ratio: 80:16
microsteps: 16
endstop_pin: !PF4
full_steps_per_rotation: 200
position_endstop: 250
position_max: 250
position_min: -160
homing_speed: 15
second_homing_speed: 3
homing_retract_dist: 0
homing_positive_dir: True

[tmc2209 stepper_z]
uart_pin: PC13
interpolate: True
run_current: 1.3
sense_resistor: 0.110
stealthchop_threshold: 0
:
[stepper_z1]
:
[tmc2209 stepper_z1]
:
```

### X/Y Stepper Test
1. With your hands, move the Gantry Bar to the center of the Y axis and the Toolhead to the center of the X axis. 
2. In the config, stepper_x corresponds to the stepper on side A. This is the one we will test first. In Mainsail > Dashboard Tab > Console Panel, type (or paste) the command: `STEPPER_BUZZ STEPPER=stepper_x`. The lower belt which is driven by stepper_x should first move toward the front of the printer. 
3. Repeat the test for stepper_y: `STEPPER_BUZZ STEPPER=stepper_y`. The upper belt on side B, driven by stepper_y should first move toward the rear of the printer.

#### Config Reference
```
printer.cfg
:
## X Stepper on Motor5 (A Motor)
[stepper_x]
dir_pin: PD7
step_pin: PG9
enable_pin: !PG11
microsteps: 32
rotation_distance: 40
full_steps_per_rotation: 200
endstop_pin: ^toolhead:LIMIT_X
position_min: 0
position_endstop: 255
position_max: 255
homing_speed: 60
homing_accel: 500
homing_retract_dist: 5
homing_positive_dir: True

[tmc5160 stepper_x]
cs_pin: PG10
spi_software_mosi_pin: PG6
spi_software_miso_pin: PG7
spi_software_sclk_pin: PG8
sense_resistor: 0.075
run_current: 2.2                         # abs max ~2.8A (stepper-limited)

## Y Stepper on Motor6 (B Motor)
[stepper_y]
dir_pin: PD3
step_pin: PD4
enable_pin: !PD6
microsteps: 32
rotation_distance: 40
endstop_pin: ^!PC15
full_steps_per_rotation: 200
position_min: 0
position_endstop: 255
position_max: 255
homing_speed: 60
homing_accel: 500
homing_retract_dist: 5
homing_positive_dir: True

[tmc5160 stepper_y]
cs_pin: PD5
spi_software_mosi_pin: PG6
spi_software_miso_pin: PG7
spi_software_sclk_pin: PG8
sense_resistor: 0.075
run_current: 2.2
```

### Extruder Stepper Test
This test is just to make sure the stepper on the Orbiter V2 Extruder is moving in the correct direction at roughly the correct speed. We will calibrate filament extrusion later.

1. Remove the Cowl.
2. Place a piece of non-transparent tape on the visible end of the extruder stepper shaft. 
3. In the Console, run `STEPPER_BUZZ STEPPER=extruder`. The tape should indicate that the stepper first rotate clockwise ~10° or a little less than 2 minute marks on an analog clock. Don't get scientific about this it's just a sanity check.
4. Remove the tape. Resist the urge to stick it on your cat.

#### Config Reference
```
printer.cfg
:
[extruder]
## Extruder movement
step_pin: toolhead:EXT_STEP
dir_pin: toolhead:EXT_DIR
enable_pin: !toolhead:EXT_EN
rotation_distance: 4.69                  # per Orbiter V2.0 Spec
microsteps: 32
full_steps_per_rotation: 200             # 1.8deg motor
:
[tmc2209 extruder]
uart_pin: toolhead:gpio15
interpolate: False
run_current: 0.85
sense_resistor: 0.110
stealthchop_threshold: 0
```

## Homing
The the mechanics of the Vertigo Mk1 require a specific homing order: Z -> Y -> X, as well as some config parameters that prepare the bed for print-related actions, like bed leveling and mesh probing.

### Z Axis Homing
To prepare for the first Z homing, each Z Joint must be lifted off its endstop so that the endstop is OPEN in the Endstops Panel in Mainsail.

1. Lift Z Joint A off its endstop and run `SET_STEPPER_ENABLE STEPPER=stepper_z` in the Console Panel. It's ok if the Bed Lever is at an angle as long as the tooling ball is below the bed contact plate. Repeat for all other Z Joints.
2. Be prepared to turn the power off or click 'Emergency Stop' at the top of the Mainsail Dashboard if the Z axes move in the wrong direction (up towards the toolhead).
3. Click the 'DEBUG HOME Z' button in the Calibration Panel in the Mainsail Dashboard.
>
>
>{: .note}
>DEBUG HOME Z is used because, as we will see and calibrate later, a standard G28 Z command will home to the endstops then raise the Front and Rear Z Joints so that the Bed Lever engages and couples to the bed contact plate.
4. Verify that the Z Joints are all at the bottom of their travel and that the endstops are triggered.

### X/Y Axis Homing
For the Vertigo, Y is always homed before X (because the filament cutter dowel extends a bit into the X travel of the toolhead). 

1. Position the Gantry Bar and Toolhead such that both endstops are OPEN in the Endstops Panel in Mainsail.
2. Be prepared to turn the power off or click 'Emergency Stop' at the top of the Mainsail Dashboard if the Z axes move in the wrong direction (up towards the toolhead).
3. Click the 'Home Y' button in the Toolhead Panel in the Mainsail Dashboard.
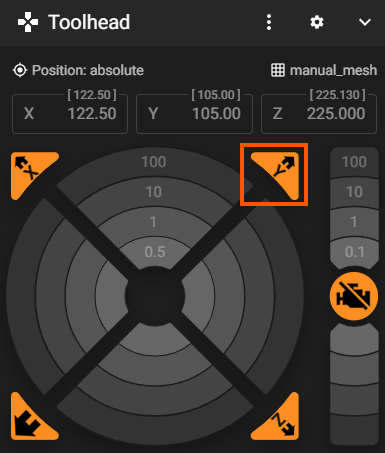
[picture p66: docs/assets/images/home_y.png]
>
1. Click the 'Home X' button in the Toolhead Panel in the Mainsail Dashboard.
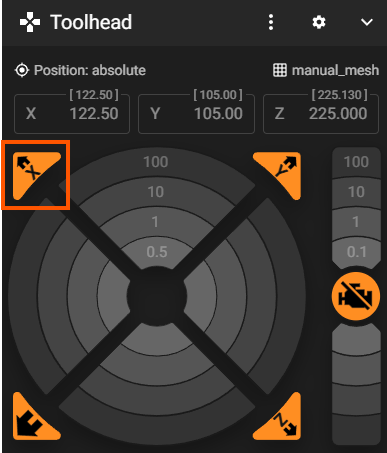
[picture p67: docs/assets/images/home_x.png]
>

### Ready Bed Position
For any operations other than clearing the bed, it is necessary to first lift the Front Z Joint Bar so that the Bed Lever is engaged. The design allows the Bed Lever to engage with the tooling ball just below the bed contact plate to avoid a loud snap and potential denting of either the ball or plate. This behavior will be examined during this calibration. Ideally the default values here are good, but it's good to check and understand what's going on.

1. If following the guide in order, the Z Joints should all be at the bottom of travel. If not, click 'DEBUG HOME Z'. Double check that all Z Joints are down on the endstops.
2. In the Console, run `FORCE_MOVE_Z_FRONT DISTANCE=1` to raise the Front Z Joint Bar up by 1mm. You will see a readout that displays the total distance moved: `front pair now +[value] mm from nominal` (so far).
3. Keep moving the Front Z Joint Bar up until the Bed Lever engages and you can see a small gap between the Bed Lever and its striker. You can use values other than 1mm to get there and dial it in.
4. Use the value in the readout `front pair now +[value] mm from nominal` for the parameter `front_engage_distance:` in printer.cfg.
5. In the Console, run `FORCE_MOVE_Z_REAR DISTANCE=1` to move the Rear Z Joints up until the tooling ball is touching the bed contact plate. The bed should be tilted slightly forward; meaning the rear of the bed is slightly higher than the front of the bed, and the Bed Wheels are not be bearing weight.
>{: .note}
>The bed must be tilted slightly forward because Z_TILT_ADJUST probes the front of the bed first, then the rear of the bed. If it is tilted the other way, it's possible that the Safety Switch will trigger during the leveling process.
6. Use the value in the readout `rear pair now +[value] mm from nominal` for the parameter `rear_couple_distance:` in printer.cfg.
7. Save printer.cfg and 'FIRMWARE RESTART' to apply changes.
8. When the interface is available again, click the normal 'Home Z' button in the Toolhead Panel. After homing to the endstops, the front and rear Z axes should move independently to couple the bed to the Front Z Joints.
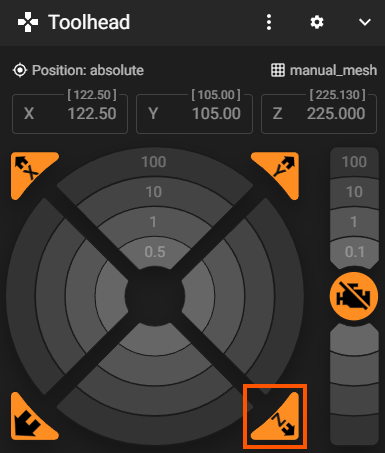
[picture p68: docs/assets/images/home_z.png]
>

#### Config Reference
```
printer.cfg
:
[vertigo_z_homing]
front_steppers: stepper_z, stepper_z1
rear_steppers: stepper_z2, stepper_z3
front_engage_distance: 25                # mm to raise the FRONT pair to engage the lever
rear_couple_distance: 13                 # mm to raise the REAR pair to couple the bed
lift_speed: 25                           # mm/s for the isolated front/rear moves (raises + jogs)
lift_accel: 100                          # mm/s^2 for the isolated front/rear moves
max_print_z: 230                         # optional explicit kinematic Z after print-home
```

### Homing Sequence
If you've gotten this far, awesome! We're getting closer to our first print. You should now not need to be so concerned with the power switch or 'Emergency Stop' button.

1. Click the 'Disable Motors' button in the Toolhead Panel in Mainsail.
>
2. Repeat step 1 of the Z Axis Homing section above to position all Z Joints above their endstops.
3. Repeat Step 1 of the X/Y Homing section above to open those endstops.
4. Now, clicking the 'Home All' or the 'Home X' button should home all axes in the proper sequence: Z -> Y -> X. Feel free to try both. Once the axes are homed, they know where they are and will then re-home independently.

#### Config Reference
```
macros.cfg
:
[homing_override]
```

## Axis Movement
Now that the printer is homed, we'll do a quick manual 'jog' to confirm the Toolhead moves nominally in X and Y and the bed moves nominally in Z -- all from the Toolhead Panel in the Mainsail Dashboard. Movement consists of concentric rings of step-size buttons (e.g. 100, 10, 1, 0.1 mm). For the toolhead (X/Y Axes), the rings are divided into 4 sections with N, E, S, W corresponding to +Y, +X, -Y, -X respectively. For the bed (Z Axis), the rings above the 'Disable Motors' button move the bed in the 'negative direction' up towards the nozzle -- counterintuitive perhaps, but this is from the perspective of the nozzle. Each click moves the selected axis by the chosen step size -- start small. Everything must be homed first; if an axis isn't homed, Mainsail will refuse the move.

### Toolhead (X/Y) Jog Test
The Toolhead moves in X and Y. After homing, the Toolhead sits at the rear-right corner (the X and Y maximums), so we'll jog *away* from there, back toward the center.

1. Confirm all axes are homed from the previous section.
2. At the bottom of the Toolhead Panel, reduce Speed Factor to 50%.
3. In the Toolhead Panel, click the '-10mm X' ring section. The Toolhead should move toward side A (left), away from the endstop. Click '+10mm X' to send it back toward side B (right).
> 
5. Repeat for Y.
>{: .important}
>Be aware of the Filament Cutter when jogging. It's possible to bump the dowel that extends into the toolhead movement area.
6. Try the other step sizes and jog each axis a little to confirm the moves feel smooth, with no grinding or skipped steps.

### Bed (Z) Jog Test
Before jogging Z, the Bed Lever must be engaged and the bed coupled to the contact plate. A standard 'Home Z' leaves the printer in exactly this state, so as long as you homed normally (not 'DEBUG HOME Z'), you're ready.

1. If the bed isn't already coupled, click 'Home Z' in the Toolhead Panel. 
> {: .warning}
>>  Whenever manually jogging the Z Axis with the Toolhead Panel, it is imperative to ensure the Bed Lever is engaged. Error checking in the `vertigo_z_homing` module should prevent jog moves from a 'decoupled' state. But you know... stuff happens. If the bed contact plate is ever above the tooling ball on the Bed Lever, do the following:  
>> - Disable Motors.
>> - Position the Front Z Joint Bar high enough above the bed contact plate to allow the Bed Lever to open.
>> - Open the Bed Lever.
>> - Move the bed or Z Joint Front Bar so that the tooling ball is below the bed contact plate. 
>> - Run a standard 'Home Z' command (G28 Z or 'Home Z' Button in Toolhead Panel). Z Axis jogging should now be 'unlocked'.  
2. Click the +1 mm button (above 'Disable Motors'). The bed should rise ~1 mm toward the nozzle.
> 
3. Click the -1 mm button (below 'Disable Motors'). The bed should lower ~1 mm away from the nozzle.
4. Move the bed up and down a few millimeters to confirm smooth, quiet travel.
> {: .warning}
>> Do not jog below where the Bed Lever touches the striker on the frame. It may not reset properly.
>
> {: .warning}
>> The 'negative' Z travel allowed for scraping means that it's possible to jog the bed up past the nozzle and into the gantry. For this test, do not move the bed within 20mm of the nozzle.
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

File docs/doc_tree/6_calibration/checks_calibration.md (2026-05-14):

---
title: Checks & Calibration
layout: default
nav_order: 6
---

# Checks & Calibration

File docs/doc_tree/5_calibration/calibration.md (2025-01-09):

---
title: Calibration
layout: default
nav_order: 5
---

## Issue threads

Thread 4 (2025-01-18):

BOM | More information about the item type

THZK100SC, 2025-01-18:
### Row 5 - Revo™ HeaterCores

Current item description: E3D Revo™ 60w HeaterCore (24V | 104-NT)
Additions:  The manufacturer offers various thermistors. It would be a good idea to include the thermistor value in the name.

Link to the producer: https://e3d-online.com/products/revo-heatercore?variant=41245338697787

AutomatedLayers, 2025-01-19:
Changed the name to reflect the E3D part number, will update in the next BOM upload (soon)

Closed 2025-01-19.

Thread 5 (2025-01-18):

.

THZK100SC, 2025-01-18:

THZK100SC, 2025-01-19:
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

An example of poor preparation. Wrong orientation of the 'Y-Endstop Cap.STL' part in the axes

AutomatedLayers, 2025-01-19:
We will reorient and add color info, but this is rather low priority at the moment. Docs/Assembly Guide will be highest prio for now.

Closed 2025-02-12.

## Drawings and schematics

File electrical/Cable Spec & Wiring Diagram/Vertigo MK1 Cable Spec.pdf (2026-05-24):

# Vertigo MK1 Cable Spec

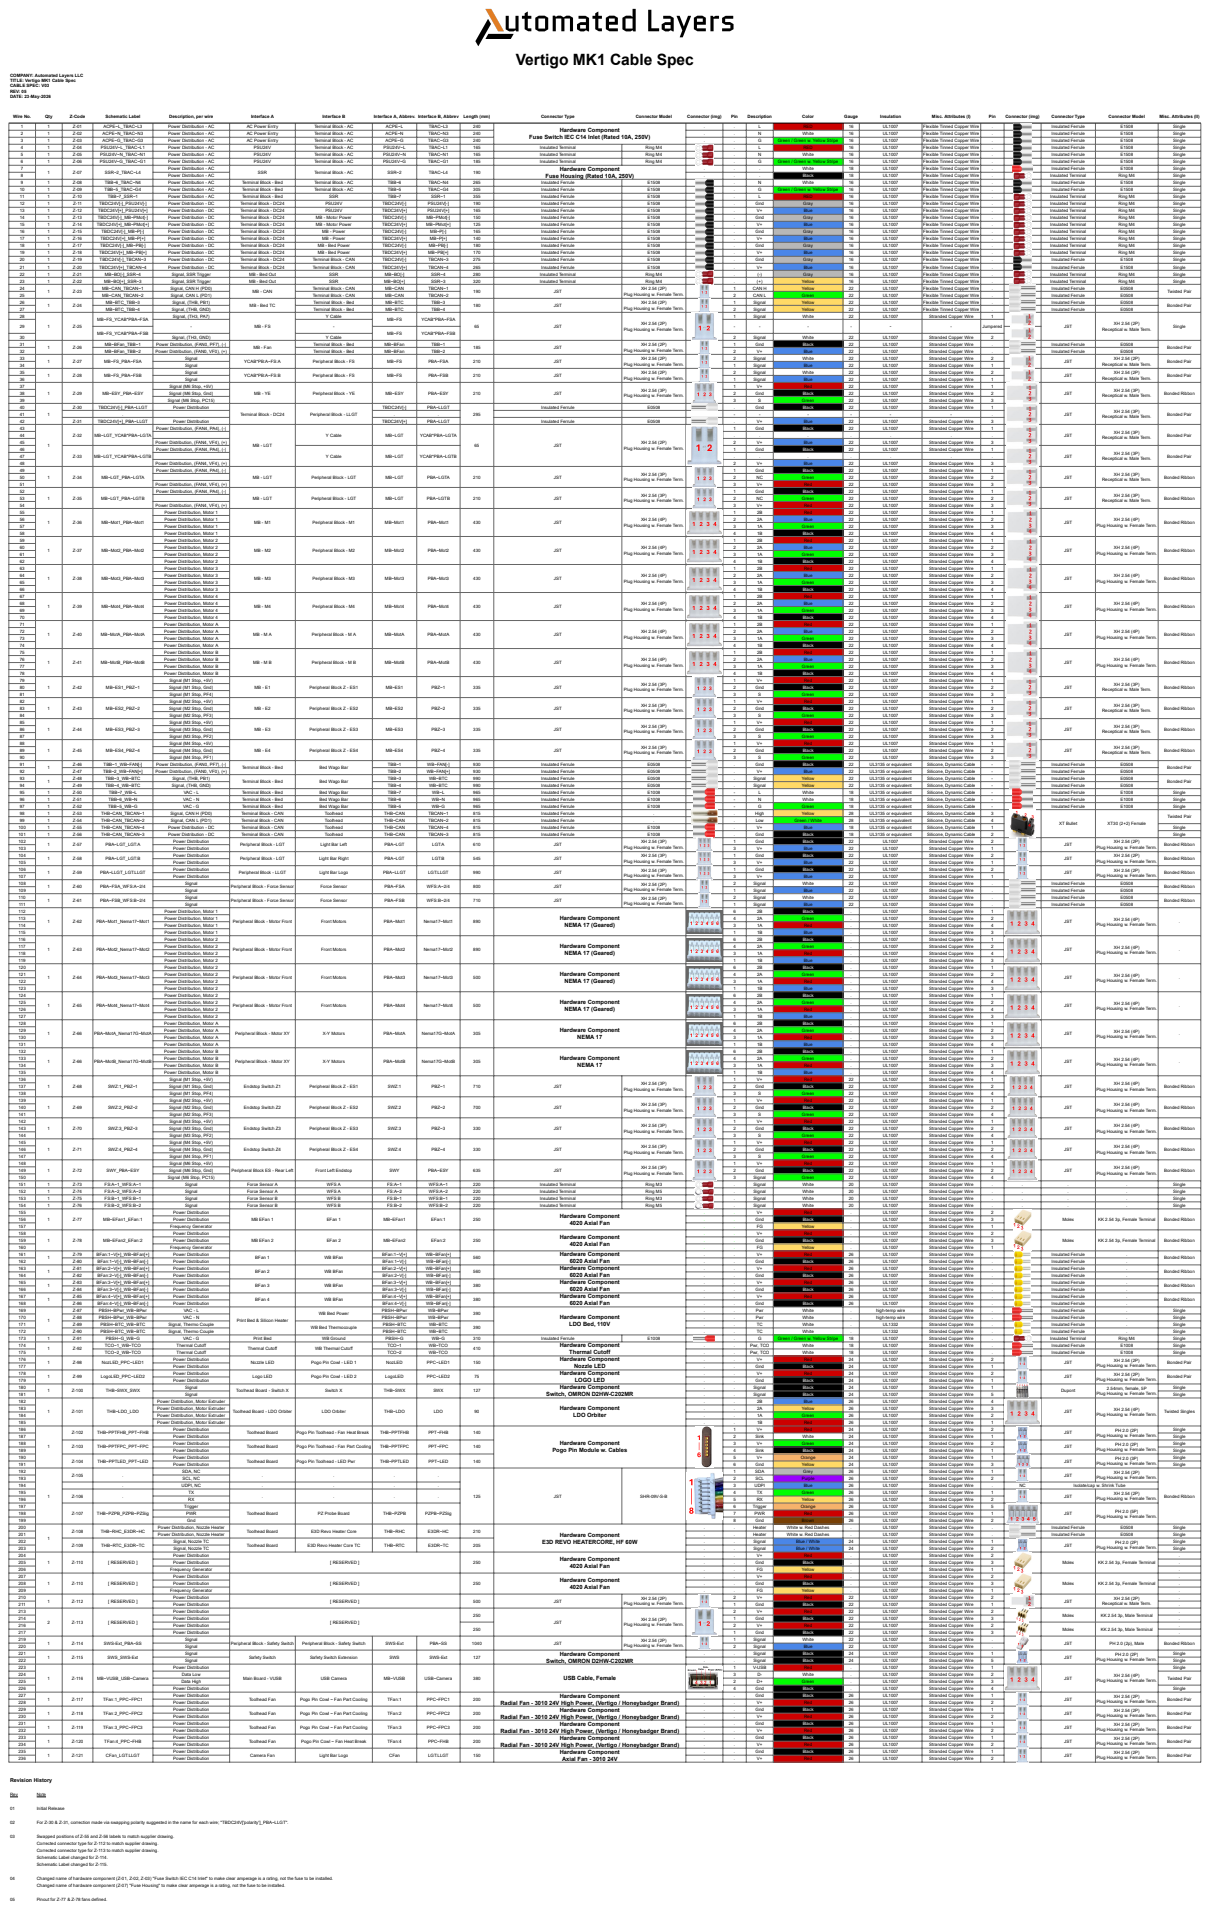
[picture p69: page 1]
Wire No.; Qty; Z-Code; Schematic Label; Description, per wire; Interface A; Interface B; Interface A, Abbrev. Interface B, Abbrev Length (mm); Connector Type; Connector Model; Connector (img); Pin; Description; Color; Gauge; Insulation; Misc. Attributes (I); Misc. Attributes (II); ACPE~L_TBAC~L3; Power Distribution - AC; AC Power Entry; Terminal Block - AC; ACPE~L; TBAC~L3; RED; Flexible Tinned Copper Wire; Insulated Ferrule; Single; ACPE~N_TBAC~N3; ACPE~N; TBAC~N3; White; ACPE~G_TBAC~G3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

COMPANY: Automated Layers LLC
TITLE: Vertigo MK1 Cable Spec
CABLE SPEC: V03
REV: 05
DATE: 23-May-2026

Power Distribution - AC

Twisted Pair

Plug Housing w. Female Term.

Bonded Pair

MB~FS_YCAB*PBA~FSA

Receptical w. Male Term.

XH 2.54 (2P) JST Bonded Pair

JST Receptical w. Male Term.

Power Distribution, Motor 1

XH 2.54 (4P) JST Bonded Ribbon

Power Distribution, Motor 2

Power Distribution, Motor 3

Power Distribution, Motor 4

Power Distribution, Motor A

Power Distribution, Motor B

XT Bullet XT30 (2+2) Female

XH 2.54 (2P) JST Bonded Ribbon

Bonded Ribbon

XH 2.54 (4P) JST .

JST Plug Housing w. Female Term.

WB Bed Power

Print Bed & Silicon Heater

Plug Housing w. Female Term. 2.54mm, female, 5P Single Dupont Plug Housing w. Female Term.

Power Distribution, Motor Extruder

XH 2.54 (4P) JST Twisted Singles

PH 2.0 (2P) Single

PH 2.0 (2P) Single JST

PH 2.0 (3P) Single JST

XH 2.54 (2P) JST

llow | 26 UL1007 Stranded Copper Wire 2

Signal, Nozzle TC
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

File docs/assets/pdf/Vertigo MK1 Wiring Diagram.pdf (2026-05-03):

# Legend

### Sequin LED

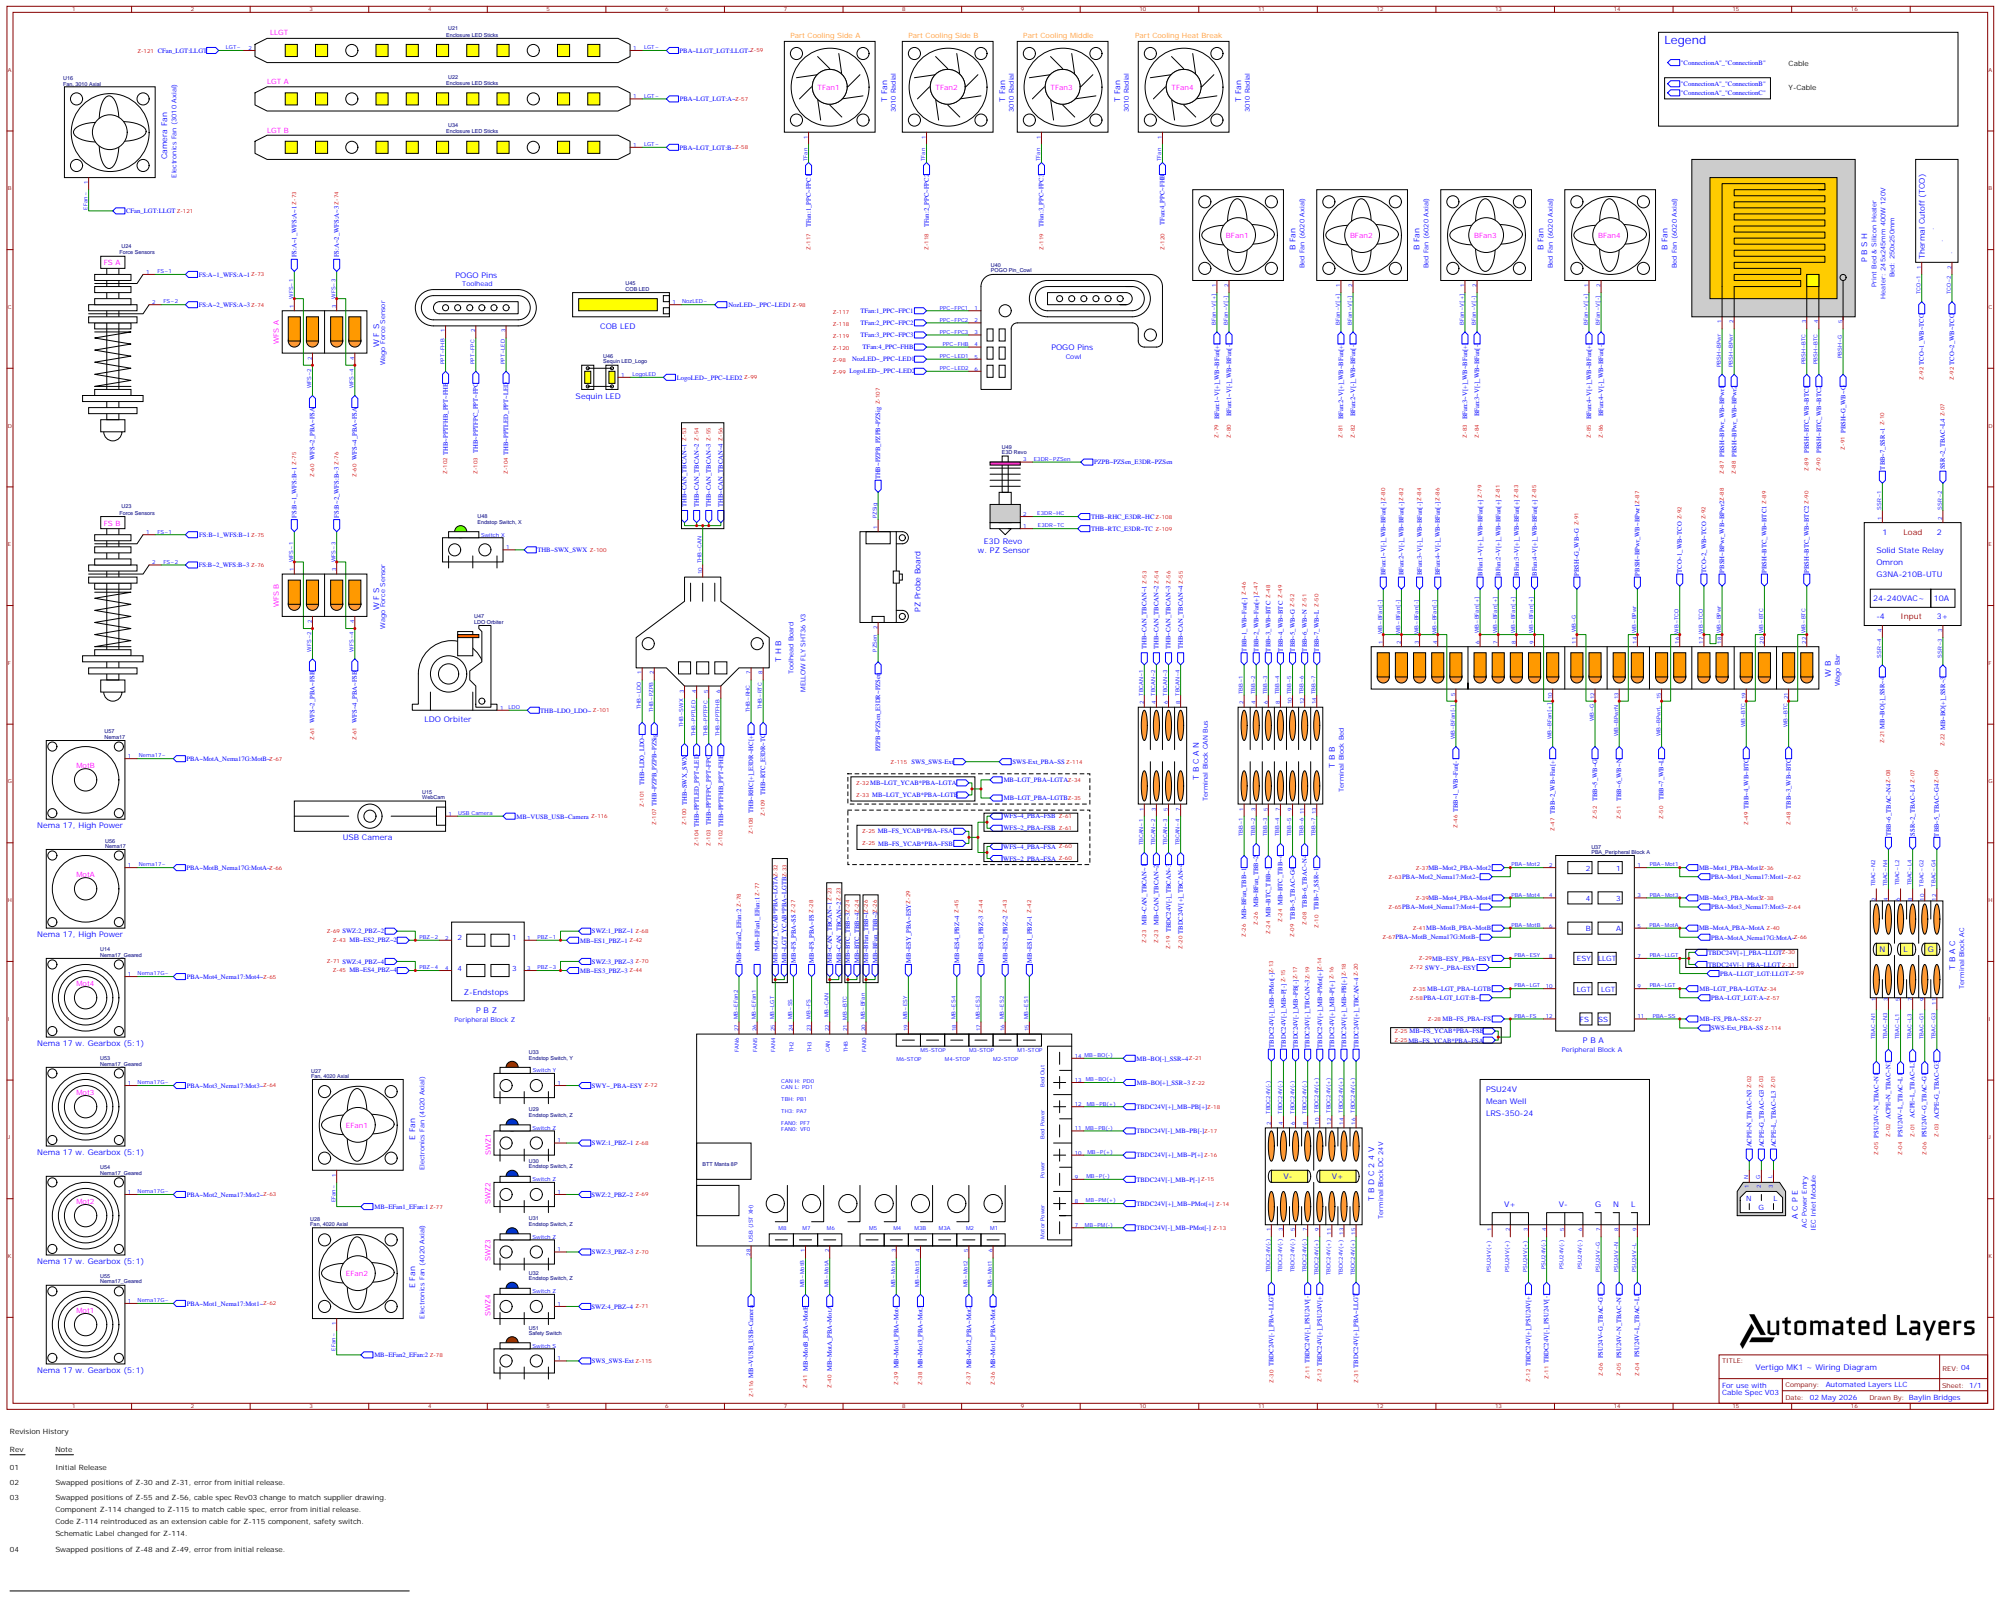
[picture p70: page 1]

Print Bed & Silicon Heater

THB~PZPB_PZPB~PZSig PZPB~PZSen_E3DR~PZSen

Terminal Block CAN Bus

Motor Power Power Bed Power Bed Out

Company: Automated Layers LLC
Date: 02 May 2026

Drawn By: Baylin Bridges

Swapped positions of Z-55 and Z-56, cable spec Rev03 change to match supplier drawing.
Component Z-114 changed to Z-115 to match cable spec, error from initial release.
Code Z-114 reintroduced as an extension cable for Z-115 component, safety switch.
Schematic Label changed for Z-114.

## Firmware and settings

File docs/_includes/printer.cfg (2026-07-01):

# ██╗   ██╗███████╗██████╗ ████████╗██╗ ██████╗  ██████╗     ███╗   ███╗██╗  ██╗ ██╗     ██████╗ ██████╗ ███╗   ██╗███████╗██╗ ██████╗ 
# ██║   ██║██╔════╝██╔══██╗╚══██╔══╝██║██╔════╝ ██╔═══██╗    ████╗ ████║██║ ██╔╝███║    ██╔════╝██╔═══██╗████╗  ██║██╔════╝██║██╔════╝ 
# ██║   ██║█████╗  ██████╔╝   ██║   ██║██║  ███╗██║   ██║    ██╔████╔██║█████╔╝ ╚██║    ██║     ██║   ██║██╔██╗ ██║█████╗  ██║██║  ███╗
# ╚██╗ ██╔╝██╔══╝  ██╔══██╗   ██║   ██║██║   ██║██║   ██║    ██║╚██╔╝██║██╔═██╗  ██║    ██║     ██║   ██║██║╚██╗██║██╔══╝  ██║██║   ██║
#  ╚████╔╝ ███████╗██║  ██║   ██║   ██║╚██████╔╝╚██████╔╝    ██║ ╚═╝ ██║██║  ██╗ ██║    ╚██████╗╚██████╔╝██║ ╚████║██║     ██║╚██████╔╝
#   ╚═══╝  ╚══════╝╚═╝  ╚═╝   ╚═╝   ╚═╝ ╚═════╝  ╚═════╝     ╚═╝     ╚═╝╚═╝  ╚═╝ ╚═╝     ╚═════╝ ╚═════╝ ╚═╝  ╚═══╝╚═╝     ╚═╝ ╚═════╝ 
                                                                                                                                     

#####################################################################
#   Includes
#####################################################################
[include mainsail.cfg]
# [include timelapse.cfg]
[include macros.cfg]

#####################################################################
#   MCUs
#####################################################################
[mcu]
canbus_uuid: 758a132d0725                # Manta8P main board

#####################################################################
#   Printer / Motion limits
#####################################################################
[printer]
kinematics: corexy
max_velocity: 1500                       # mm/s
max_accel: 40000                         # mm/s^2
max_z_velocity: 30                       
max_z_accel: 100
square_corner_velocity: 5.0

#####################################################################
#   Host features
#####################################################################
[respond]                                # lets macros print messages to the console

[save_variables]
filename: ~/printer_data/config/config_variables.cfg

[force_move]
enable_force_move: True                  # required by the trapq subset moves (scrape / vertigo homing)

[idle_timeout]
timeout: 6000
gcode:
    TURN_OFF_HEATERS
    DETACH_PROBE                         # NOTE: define this (or remove) -- not in macros.cfg; smart_effector has no dock
    M84

[delayed_gcode on_startup]
initial_duration: 1.0
gcode:
    RESPOND MSG="Welcome to Vertigo!"
    _MACRO_VARIABLES                     # runs once -> converts the mm/s speed vars to mm/min

[exclude_object]                         # object exclusion (cancel individual objects mid-print)

[pause_resume]                           # backs PAUSE/RESUME (used by the scrape-fail prompt + mainsail)

[gcode_arcs]
resolution: 0.2

[input_shaper]
shaper_type_x = mzv
shaper_type_y = mzv
shaper_freq_x = 66.4
shaper_freq_y = 47.0

# [filament_switch_sensor filament]
# pause_on_runout: True
# switch_pin: PF0

#####################################################################
#   X / Y Stepper Settings
#####################################################################
## X Stepper on Motor5 (A Motor)
[stepper_x]
dir_pin: PD7
step_pin: PG9
enable_pin: !PG11
microsteps: 32
rotation_distance: 40
full_steps_per_rotation: 200
endstop_pin: ^toolhead:LIMIT_X
position_min: -2.5
position_endstop: 251
position_max: 252.5
homing_speed: 60
homing_accel: 500
homing_retract_dist: 5
homing_positive_dir: True

[tmc5160 stepper_x]
cs_pin: PG10
spi_software_mosi_pin: PG6
spi_software_miso_pin: PG7
spi_software_sclk_pin: PG8
sense_resistor: 0.075
run_current: 2.2                         # abs max ~2.8A (stepper-limited)

## Y Stepper on Motor6 (B Motor)
[stepper_y]
dir_pin: PD3
step_pin: PD4
enable_pin: !PD6
microsteps: 32
rotation_distance: 40
endstop_pin: ^!PC15
full_steps_per_rotation: 200
position_min: -35
position_endstop: 220
position_max: 221
homing_speed: 60
homing_accel: 500
homing_retract_dist: 5
homing_positive_dir: True

[tmc5160 stepper_y]
cs_pin: PD5
spi_software_mosi_pin: PG6
spi_software_miso_pin: PG7
spi_software_sclk_pin: PG8
sense_resistor: 0.075
run_current: 2.2

#####################################################################
#   Z Stepper Settings (4 independent Z; standard enable_pins)
#####################################################################
# FRONT pair = stepper_z (front-left) + stepper_z1 (front-right), joined by the
# flexible lever bar. REAR pair = stepper_z2 (rear-left) + stepper_z3 (rear-right).
# Endstops are at the BOTTOM of travel. Up = NEGATIVE Z. See [vertigo_z_homing].

## Z0 Stepper - Front Left
[stepper_z]
dir_pin: PE5
step_pin: PE6
enable_pin: !PC14                        # active-low EN (was output_pin _z0_en)
rotation_distance: 40
gear_ratio: 80:16
microsteps: 16
endstop_pin: !PF4
full_steps_per_rotation: 200
position_endstop: 250
position_max: 250
position_min: -153
homing_speed: 15
second_homing_speed: 3
homing_retract_dist: 0
homing_positive_dir: True

[tmc2209 stepper_z]
uart_pin: PC13
interpolate: True
run_current: 1.3
sense_resistor: 0.110
stealthchop_threshold: 0

## Z1 Stepper - Front Right
[stepper_z1]
dir_pin: !PE1
step_pin: PE2
enable_pin: !PE4                         # active-low EN (was output_pin _z1_en)
rotation_distance: 40
gear_ratio: 80:16
microsteps: 16
endstop_pin: !PF3
full_steps_per_rotation: 200

[tmc2209 stepper_z1]
uart_pin: PE3
interpolate: True
run_current: 1.3
sense_resistor: 0.110
stealthchop_threshold: 0

## Z2 Stepper - Rear Left
[stepper_z2]
dir_pin: PB7
step_pin: PB8
enable_pin: !PE0                         # active-low EN (was output_pin _z2_en)
rotation_distance: 40
gear_ratio: 80:16
microsteps: 16
endstop_pin: !PF2
full_steps_per_rotation: 200

[tmc2209 stepper_z2]
uart_pin: PB9
interpolate: True
run_current: 1.3
sense_resistor: 0.110
stealthchop_threshold: 0

## Z3 Stepper - Rear Right
[stepper_z3]
dir_pin: !PB3
step_pin: PB4
enable_pin: !PB6                         # active-low EN (was output_pin _z3_en)
rotation_distance: 40
gear_ratio: 80:16
microsteps: 16
endstop_pin: !PF1
full_steps_per_rotation: 200

[tmc2209 stepper_z3]
uart_pin: PB5
interpolate: True
run_current: 1.3
sense_resistor: 0.110
stealthchop_threshold: 0

#####################################################################
#   Temperature Monitoring (main board)
#####################################################################
[temperature_sensor Manta8P_MCU]
sensor_type: temperature_mcu

[temperature_sensor CB1_HOST]
sensor_type: temperature_host

#####################################################################
#   Toolhead Board (CAN)
#####################################################################
[mcu toolhead]
canbus_uuid: 5db058c66e4a

## Board pin aliases
[board_pins toolhead]
mcu: toolhead
aliases:
aliases_step:
    EXT_EN=gpio14,
    EXT_STEP=gpio7,
    EXT_DIR=gpio6,
    EXT_UART=gpio15
aliases_limitsw:                         # preferred for endstops (incl. klicky)
    # LIMIT_X=gpio20,
    LIMIT_X=gpio22,
    PROBE_TRIGGER=gpio16
aliases_fans:
    FAN1=gpio13,
    FAN0=gpio21
aliases_thermistors:
    TH0=gpio27,
    # EXT_TEMP_CS=gpio17,
    # EXT_TEMP_SCLK=gpio2,
    # EXT_TEMP_MISO=gpio4,
    # EXT_TEMP_MOSI=gpio3
aliases_heaters:
    EXT_HEATER=gpio23
aliases_rgb:
    RGBLED=gpio26
aliases_lis2dw:
    ADXL_CS=gpio12,
    ADXL_SCLK=gpio2,
    ADXL_MISO=gpio4,
    ADXL_MOSI=gpio3

## Toolhead MCU temperature
[temperature_sensor toolhead]
sensor_type: temperature_mcu
sensor_mcu: toolhead

#####################################################################
#   Accelerometer / Resonances
#####################################################################
## https://docs.kalico.gg/Measuring_Resonances.html
[lis2dw]
cs_pin: toolhead:gpio12
spi_software_sclk_pin: toolhead:gpio2
spi_software_mosi_pin: toolhead:gpio3
spi_software_miso_pin: toolhead:gpio4

[resonance_tester]
accel_chip: lis2dw
probe_points: 150, 150, 20               # slightly above the middle of the bed
min_freq: 5
max_freq: 133
accel_per_hz: 75
hz_per_sec: 1

#####################################################################
#   Extruder
#####################################################################
## https://www.klipper3d.org/Config_Reference.html#extruder
[extruder]
## Extruder movement
step_pin: toolhead:EXT_STEP
dir_pin: toolhead:EXT_DIR
enable_pin: !toolhead:EXT_EN
rotation_distance: 4.69                  # per Orbiter V2.0 Spec
microsteps: 32
full_steps_per_rotation: 200             # 1.8deg motor
max_extrude_only_distance: 500
max_extrude_only_velocity: 120
max_extrude_only_accel: 10000            # default 8000
nozzle_diameter: 0.400
filament_diameter: 1.750
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

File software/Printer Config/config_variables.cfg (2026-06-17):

#  ██████╗ ██████╗ ███╗   ██╗███████╗██╗ ██████╗     ██╗   ██╗ █████╗ ██████╗ ██╗ █████╗ ██████╗ ██╗     ███████╗███████╗
# ██╔════╝██╔═══██╗████╗  ██║██╔════╝██║██╔════╝     ██║   ██║██╔══██╗██╔══██╗██║██╔══██╗██╔══██╗██║     ██╔════╝██╔════╝
# ██║     ██║   ██║██╔██╗ ██║█████╗  ██║██║  ███╗    ██║   ██║███████║██████╔╝██║███████║██████╔╝██║     █████╗  ███████╗
# ██║     ██║   ██║██║╚██╗██║██╔══╝  ██║██║   ██║    ╚██╗ ██╔╝██╔══██║██╔══██╗██║██╔══██║██╔══██╗██║     ██╔══╝  ╚════██║
# ╚██████╗╚██████╔╝██║ ╚████║██║     ██║╚██████╔╝     ╚████╔╝ ██║  ██║██║  ██║██║██║  ██║██████╔╝███████╗███████╗███████║
#  ╚═════╝ ╚═════╝ ╚═╝  ╚═══╝╚═╝     ╚═╝ ╚═════╝       ╚═══╝  ╚═╝  ╚═╝╚═╝  ╚═╝╚═╝╚═╝  ╚═╝╚═════╝ ╚══════╝╚══════╝╚══════╝

# These variables are used to configure the behavior of your specific printer and its associated macros. A separate file is used so that updates
# to macros.cfg will not affect these custom settings.

[gcode_macro _MACRO_VARIABLES]
# ---- Speeds ----
# NOTE: declared in mm/s, then converted to mm/min (x60) in this macro's gcode
# below so they can be used directly as F values. That conversion only happens
# when _MACRO_VARIABLES is RUN, so it must execute once at startup (e.g. from a
# [delayed_gcode] or your first home) or these will still be in mm/s.
variable_speed_xy: 250                          # mm/s -> mm/min after conversion
variable_speed_z: 25                            # mm/s -> mm/min after conversion
variable_fast_acc: 12000                        # mm/s^2
variable_slow_acc: 2000                         # mm/s^2
variable_speed_extrude: 5                       # mm/s -> mm/min after conversion
variable_speed_unload: 20                       # mm/s

# ---- Default temperatures (C) ----
variable_default_temp_extruder: 230             
variable_default_temp_bed: 55
variable_default_temp_vitrification: 60

# ---- PID tuning temperatures (C) ----
variable_pid_extruder_temps: [200, 220, 240, 260, 270]
variable_pid_bed_temps: [55, 70, 85, 105]

# ---- Filament load prompt temperatures (material, C) ----
variable_load_temps: [["PLA", 220], ["PETG/TPU", 240], ["ABS/ASA", 260], ["PC/PA", 270]]

# ---- Nozzle prime settings ----
variable_prime_pos_x: 1
variable_prime_pos_y: 40
variable_prime_pos_z: 0.1
variable_prime_layer_z_height: 0.3

# ---- Bed scrape settings ----
variable_scrape_max_temp_threshold_default: 35

# ---- Filament cutter settings ----
variable_cut_pos_x: 249.5
variable_cut_pos_y: 18
variable_cut_attach_y_dist: 20
variable_cut_dx: 22
variable_cut_dy: 23

# ---- Purge / wipe / plug settings ----
variable_plug_pos_x: 18
variable_plug_pos_y: -29
# variable_purge_pos_x: 0 #TO BE IMPLEMENTED
# variable_purge_pos_y: 5 #TO BE IMPLEMENTED                
variable_wipe_dist: 15
variable_wipe_speed: 50                          # mm/s -> mm/min after conversion
# variable_purge_dist: 125 #TO BE IMPLEMENTED
# variable_purge_speed: 5 #TO BE IMPLEMENTED                         # mm/s -> mm/min after conversion
variable_wipe_plug_dx: 12.1

# ---- Orca curr_bed_type -> surface token ----
variable_bed_type_map: {"Smooth Cool Plate": "smooth_cool", "Textured Cool Plate": "textured_cool", "Engineering Plate": "engineering", "High Temp Plate": "high_temp", "Textured PEI Plate": "textured_pei", "Cool Plate (SuperTack)": "super_tack"}

# ---- Per-surface / per-temp bed mesh ----
variable_default_surface: "textured_pei"
variable_mesh_temps: [55, 70, 85, 100]
variable_mesh_soak_minutes: 0

# ---- Adaptive bed mesh ----
variable_adaptive_mesh: False      # True -> PRINT_START always adaptive-meshes (ignores per-surface profiles & the prompt)
variable_adaptive_margin: 5        # mm margin around the print area when adaptive

# ---- Timelapse settings ----
# variable_print_timelapse_enabled: False #TO BE IMPLEMENTED
# variable_scrape_timelapse_enabled: False #TO BE IMPLEMENTED

gcode:
    # Dump every variable to the console for quick inspection.
    {% set macro_vars = printer["gcode_macro _MACRO_VARIABLES"] %}
    {% set out = [] %}
    {% for param, value in macro_vars.items() %}
        {% set dummy = out.append("| %s: %s" % (param, value)) %}
    {% endfor %}
    {action_respond_info("Macro Variables:\n" + out|join("\n"))}

    # ---- Convert the mm/s speeds above into mm/min for F-word use ---- #
    # *** DO NOT CHANGE *** (runs once; see the speeds NOTE above)
    SET_GCODE_VARIABLE MACRO=_MACRO_VARIABLES VARIABLE=speed_xy           VALUE={(macro_vars.speed_xy * 60)}
    SET_GCODE_VARIABLE MACRO=_MACRO_VARIABLES VARIABLE=speed_z            VALUE={(macro_vars.speed_z * 60)}
    SET_GCODE_VARIABLE MACRO=_MACRO_VARIABLES VARIABLE=speed_extrude      VALUE={(macro_vars.speed_extrude * 60)}
    SET_GCODE_VARIABLE MACRO=_MACRO_VARIABLES VARIABLE=wipe_speed         VALUE={(macro_vars.wipe_speed * 60)}
    # SET_GCODE_VARIABLE MACRO=_MACRO_VARIABLES VARIABLE=purge_speed        VALUE={(macro_vars.purge_speed * 60)}
    SET_GCODE_VARIABLE MACRO=_CLIENT_VARIABLE VARIABLE=custom_park_x        VALUE={macro_vars.plug_pos_x}
    SET_GCODE_VARIABLE MACRO=_CLIENT_VARIABLE VARIABLE=custom_park_y        VALUE={macro_vars.plug_pos_y}
    SET_GCODE_VARIABLE MACRO=_CLIENT_VARIABLE VARIABLE=park_at_cancel_x        VALUE={macro_vars.plug_pos_x}
    SET_GCODE_VARIABLE MACRO=_CLIENT_VARIABLE VARIABLE=park_at_cancel_y        VALUE={macro_vars.plug_pos_y}

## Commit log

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2025-01-11 fixing image case
2025-01-13 update 1_frame.md
    frame assy page mostly complete.
    [Frame.obj, frame-1.obj]
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2025-01-19 Update and rename BOM.csv to BOM.md
    [BOM.csv]
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2025-01-31 Added Toolhead Plate STEPs
    [Toolhead Plate - CNC - Mild Steel 1045 - No Pockets.STEP, Toolhead Plate - CNC - Mild Steel 1045.STEP]
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2025-03-01 Adding DXF folder with DXF files
    [Acrylic Side Panel_Q2.DXF, Door Panel.DXF, Electronics Panel Cover.DXF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]
2025-03-05 Changed out no-pocket toolhead plate .STEP with a larger tolerance .STEP. Also added a drawing for the no-pocket .STEP
    [Toolhead Plate - CNC - Mild Steel 1045 - No Pockets.STEP]
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2025-03-07 Relaxed Tolerances & Fixed Drawing's Hole Callout
    [Toolhead Plate - CNC - Mild Steel 1045 - No Pockets.STEP, Toolhead Plate - CNC - Mild Steel 1045 - Pockets.STEP, Toolhead Plate - CNC - Mild Steel 1045.STEP]
2025-03-27 Removed STLs, Will upload as revalidated
    [Bed Frame_E-Chain Bed Mount.STL, Bed Frame_Fan Mount_Q4.STL, Bed Frame_Flow Blocker Clip_Q7.STL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]
2025-03-27 STLs Validated: Electronics Backpack & Frame
    [AC Power Plug DIN Clip Adapter.stl, DIN Rail Clip - Q14.stl, Electronics Backpack Base A.stl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]
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2025-06-15 Create Tool - Rear Bar Alignment.STL
    [Tool - Rear Bar Alignment.STL]
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2025-06-23 Audited Kinematics & XY Gantry
    [Belt Clamp Bottom_9mm_Q4.stl, Belt Clamp Top_9mm_Q4.stl, Front Joint A_Endstop Adjustment.stl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]
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2025-06-27 Create Idler Bearing Tool.stl
    [Idler Bearing Tool.stl]
2025-06-27 Fixed tolerance issue for Toolhead Plate, Omron Sw interface. New drawing + STEP release.
    [Toolhead Plate - CNC - Mild Steel 1045 - No Pockets - REV C.STEP, Toolhead Plate - CNC - Mild Steel 1045 - No Pockets.STEP, Toolhead Plate - CNC - Mild Steel 1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]
2025-06-27 Fixed XY Joint extrusion endstop. Adding Toolhead Carriage Block.
    [Light Bar Offset Tool.STL, XY Joint B - Bottom.stl]
2025-06-28 Added most of the peripherals
    [Cable Routing B Cap.stl, Cable Routing B.stl, Extrusion Clip 10mm - Q4.stl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]
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2025-06-30 Fixed Y endstop & Cable Routing models. Adding Force sensor washer set tool.
    [Cable Routing B Cap.stl, Cable Routing B.stl, Force Sensor Washer Setting Tool.stl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]
2025-06-30 Added top module. Fixed rear panel top corners. Added new clips.
    [Extrusion Clip - Cable Gutter 105mm.stl, Extrusion Clip - Cable Gutter 125mm.stl, Extrusion Clip - Z Endstop Center Cable Gutter.stl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]
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2025-07-02 Update SSR Mount & Fuse Holder.stl
    [SSR Mount & Fuse Holder.stl]
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2025-07-04 Toolhead Cowl PCB V0.4, fixed silkscreen.
2025-07-06 Create Fan Screw Spacer - Q2.stl
    [Fan Screw Spacer - Q2.stl]
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2025-07-10 Added Bed STLS and updated rear Z-joint seatbelt locks
    [Bed E-Chain Mount - Clip.stl, Bed E-Chain Mount - Frame.stl, Bed Frame - Fan Mount - Q4.stl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]
2025-07-11 Fixed WAGO Bar
    [Safety Switch Bracket.stl]
2025-07-13 Fixed names
    [Scraper Bar Height Adjustment Block - Accent - Q2.stl, Scraper Bar Wing_Frame Wedge A - Accent.stl, Scraper Bar Wing_Frame Wedge B - Accent.stl]
2025-07-14 Toolhead Plate Rev D
    [Toolhead Plate - CNC - Mild Steel 1045 - No Pockets - REV C.STEP, Toolhead Plate - CNC - Mild Steel 1045 - No Pockets - REV D.STEP]
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2025-07-17 Updated Z-Drive Housing Caps to accept M3x10 thumb screw
    [Z Drive Housing Cap A - Q2.stl, Z Drive Housing Cap B - Q2.stl]
2025-07-17 Rolling Toolhead Plate back to REV C
    [Toolhead Plate - CNC - Mild Steel 1045 - No Pockets - REV C.STEP, Toolhead Plate - CNC - Mild Steel 1045 - No Pockets - REV D.STEP]
2025-07-28 Bed Chain Cable Setter + Updated E-Chain Mount - Clip
    [Bed Chain Cable Setter Tool.STL, Bed E-Chain Mount - Clip.stl, Bed E-Chain Mount - Frame.stl]
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2025-10-23 added XY Drive Roll-in Nut Alignment Tool
    [AC Power Plug DIN Clip Adapter.stl, AFC.cfg, AFC_Hardware.cfg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]
2025-10-23 Updated Tool Ball Mounts ~ Prevents disengagement from front tool ball.
    [Bed Frame - Tool Ball Mount A.stl, Bed Frame - Tool Ball Mount B.stl]
2025-10-25 Rename XY_Drives_Roll_Nut_Alignment.STL to XY Drives Roll-In Nut Alignment.STL
    [XY Drives Roll-In Nut Alignment.STL]
2025-10-25 Added Orca Slicer config and STL
    [PrintBed_w_CoordinateSys.STL]
2025-10-26 Fixed XY Drive Nut Alignment Tool STL Orientation
    [Foot Front - Roll-In Nut Alignment Tool.STL, Foot Rear - Roll-In Nut Alignment Tool.STL, XY Drives Roll-In Nut Alignment.STL]
2025-10-26 Rename Extrusion Clip - Cable Gutter 105mm - Q2.stl to Cable Gutter 105mm - Q2.stl
    [Cable Gutter 105mm - Q2.stl]
2025-10-26 Rename Extrusion Clip - Z Endstop Center Cable Gutter.stl to Cable Gutter - Z Endstop Center.stl
    [Cable Gutter - Z Endstop Center.stl]
2025-10-26 Rename Extrusion Clip 10mm - Q4.stl to Cable Cover 10mm - Q4.stl
    [Cable Cover 10mm - Q4.stl]
2025-10-26 Rename Extrusion Clip 240mm - Q2.stl to Cable Cover 240mm - Q2.stl
    [Cable Cover 240mm - Q2.stl]
2025-10-26 Rename Extrusion Clip 25mm - Q4.stl to Cable Cover 25mm - Q4.stl
    [Cable Cover 25mm - Q4.stl]
2025-10-26 Rename Extrusion Clip 55mm - Q2.stl to Cable Cover 55mm - Q2.stl
    [Cable Cover 55mm - Q2.stl]
2025-10-26 Rename Y-Endstop.stl to Y-Endstop Pod.stl
    [Y-Endstop Pod.stl]
2025-10-26 Rename Y-Endstop Pod.stl to Y Endstop Pod.stl
    [Y Endstop Pod.stl]
2025-10-26 Rename Y-Endstop Cap.stl to Y Endstop Pod Cap.stl
    [Y Endstop Pod Cap.stl]
2025-10-26 Rename Cable Routing B.stl to Cable Routing Pod B.stl
    [Cable Routing Pod B.stl]
2025-10-26 Rename Cable Routing B Cap.stl to Cable Routing Pod B Cap.stl
    [Cable Routing Pod B Cap.stl]
2025-10-26 Added Slicer Config Files
    [PrintBed_w_CoordinateSys.STL]
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2025-11-02 Organizational updates, Top Fan Grill update
    [Facade Frame Front - Accent.stl, Facade Frame Front Insert - Transparent.stl, Facade Side A.stl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]
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2025-11-06 Small fix for XY joints
    [XY Joint A - Bottom.stl, XY Joint B - Bottom.stl]
2025-11-08 Wheel Ramp, Safety Switch, E-Backpack
    Improved Wheel Ramps, Safety Switch location change, E-Backpack update to allow higher DIN rail tolerance
    [Electronics Backpack Base A.stl, Electronics Backpack Base B.stl, Electronics Backpack Side A S2.stl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]
2025-11-08 Fixed Print Orientation
    [Frame Post Connector - Q2.STL]
2025-11-08 Name Change, missing "accent"
    [Belt Clamp Bottom_9mm - Accent - Q4.stl, Belt Clamp Top_9mm - Accent - Q4.stl]
2025-11-10 Fixed naming and orientation
    [Fan Grill - Optional - Q2.STL, Front Joint_Spherical Bearing Block - Accent - Q2.stl]
2025-11-18 Update Panel Latch - Add Support - Q18.stl
    Added small angle bias to help with tolerances.
2025-11-19 Fixed depth of logo - Still needs fix in CAD
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2025-11-19 Added LDO kit profile
    New STL added for LDO's 2020 extrusion
    [Frame Post Connector - Q2 (LDO Profile).STL, Frame Post Connector - Q2 (Old).STL]
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2026-02-17 Replace Force Sensor Frame Mount A/B STLs with versions that include cable routing
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2026-04-13 Update Foot Height Knob Cap - Accent - Q4.stl
    [Foot Height Knob Cap - Accent - Q4.stl]
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2026-04-17 Sync: copy updated files from 'software/Printer Config' to 'docs/assets/config' (preserve subdirs)
    [printer.cfg]
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2026-05-07 update foot with short knob cap option
    [ALTERNATIVE-SHORT - Foot Height Knob Cap - Accent - Q4 .stl]
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2026-05-11 XY Joints - Minor FIxes from Steve's build
    - Slightly tighter insert holes to match rest of printer standard
    - lower height of extrusion slot index feature to allow roll-in nuts to slide under easier
    [XY Joint A - Bottom.stl, XY Joint A - Top.stl, XY Joint B - Bottom.stl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]
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2026-05-11 Rename Foot Rear A Base.STL to Foot Rear A Base.stl
    [Foot Rear A Base.stl]
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2026-05-11 made extrusion slot index a bit shorter
    [XY Joint A - Top.stl, XY Joint B - Top.stl]
2026-05-11 Rename XY Joint B - Endstop Touchoff - Accent.stl to XY Joint B - Endstop Block - Accent.stl
    [XY Joint B - Endstop Block - Accent.stl]
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2026-05-14 Updated Assembly Video - XY Idlers - Fixed orientation of M3 roll-in nuts
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2026-05-19 Update Foot Rear A Base.stl
    fixed corrupt file
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2026-05-22 55mm cable cover qty fix, added routing pod as separate section, bit better organization
    also updated some hw and printed parts tables
    [Cable Cover 55mm - Q8.stl, Cable Routing Pod.stl]
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2026-06-04 Sync: copy cfg to _includes and PDFs to assets/pdf
    [printer.cfg]
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2026-06-13 Lots of calibration page updates
    also mainsail dashboard edit and and fixed broken stl links in scraper bar
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2026-06-15 big config updates to match new vertigo kalico modules
    and general macro improvements, particularly with bed mesh and filament specific offsets
    [macros.cfg, printer.cfg]
2026-06-17 release with vertigo_z_homing, force_sensor_probe, macro updates, and separate config variables file
    [config_variables.cfg, macros.cfg, printer.cfg]
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
